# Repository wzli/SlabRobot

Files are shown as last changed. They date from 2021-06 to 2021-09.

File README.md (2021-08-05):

# Slab Robot
Work in progress...

## Mechanical Design
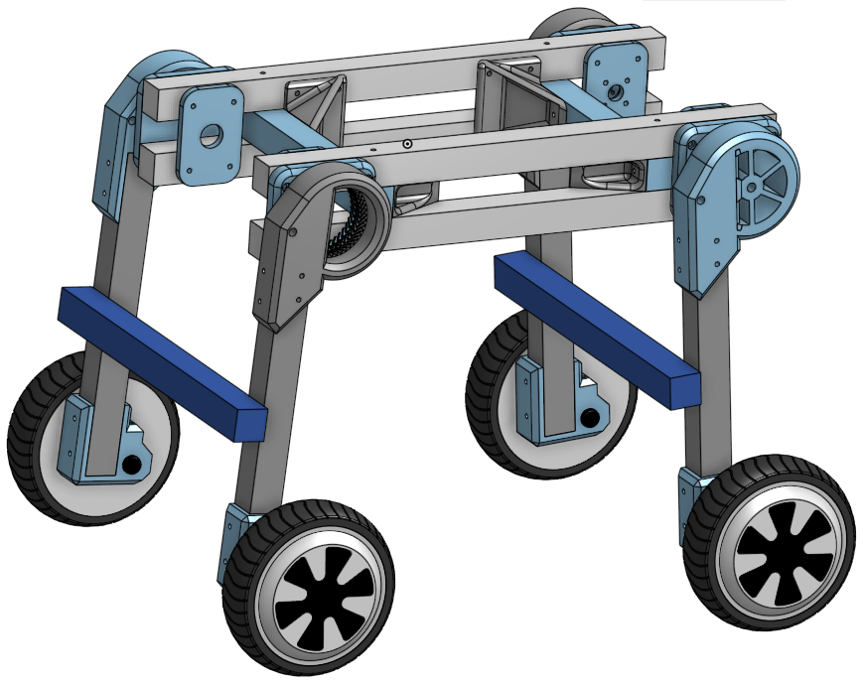
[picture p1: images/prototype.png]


[OnShape CAD Document](https://cad.onshape.com/documents/01b7bf47ac0296002ad3efc0/w/656ec7f127d0c64f6943908d/e/5454fd1cd4994d1435836e10)

## Simulation
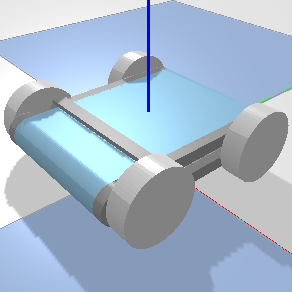
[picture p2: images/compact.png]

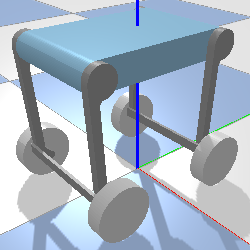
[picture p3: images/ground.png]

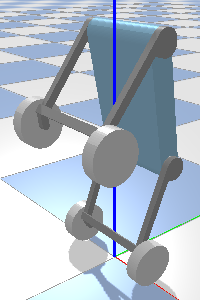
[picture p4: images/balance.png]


[Onshape to Robot](https://onshape-to-robot.readthedocs.io/) is used to generate robot simulation URDF files based on the concept assembly CAD.

```bash
# generate urdf
sudo apt install openscad meshlab # install system dependencies
pip install onshape-to-robot # install python application

# generate and output to urdf directory based on urdf/config.json
onshape-to-robot urdf
```

Run the following commands (or the equivalent on your system) to setup:

```bash
# install system dependencies
sudo apt install cmake gcc python3
# Install pytohn dependencies:
pip3 install -r requirements.txt

# Build libslab
mkdir libslab/build
(cd libslab/build && cmake .. && make)
```

To start, execute `./sim.py`. A connected USB gamepad is required.

The controls are:

- Home button resets simulation.
- Select button recenters camera.
- Left stick controls wheels.
  - X-axis controls turning velocity.
  - Y-axis controls forward velocity.
  - D-pad scaled by L-trigger maps to left stick controls.
- Right stick controls legs.
  - X-axis controls rotation of both legs in the same direction.
  - Y-axis controls rotation of both legs in different directions (when not balancing).
  - Y-axis controls body incline (when balancing).
  - Diagonal axis controls individual legs.
  - Buttons scaled by R-trigger maps to right stick controls.
- Holding R button maps right stick to leg position presets.
  - Up maps U preset.
  - Down maps to inverted U preset.
  - Left maps to fully unfolded preset.
  - Right maps to fully folded preset.
- Holding L button disables balance controller.
- Balance controller automatically engages when one pair of legs are detected to be off the ground.

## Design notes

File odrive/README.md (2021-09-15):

# ODrive Setup Guide

Tips on setting up Odrive (v3.6) on FW v5.2 complementary to the [Official Docs](https://docs.odriverobotics.com/).

# USB connection
See [Downloading and Installing Tools](https://docs.odriverobotics.com/#downloading-and-installing-tools).

- For linux, need to setup udev rules.
- For windows, need to use [zadig](https://zadig.akeo.ie) to setup *libusb-win32* driver.

# Firmware
Should first update to latest firmware by running `odrivetool dfu`.
See [docs](https://docs.odriverobotics.com/#firmware) for details.
If that runs into issues though, don't bother troubleshooting *dfu* it's way more simple and reliable to just build firmware and flash through STlink.

## Firmware Development
Refer to [docs](https://docs.odriverobotics.com/developer-guide), in summary:

- Install dependencies `gcc-arm-embedded, openocd, tup, etc`.
- `git clone https://github.com/odriverobotics/ODrive` and pull the latest release.
- Edit `Firmware/tup.config` and call `make` in Firmware directory.
- Connect STlink pins `GND, SWD, and SWC` and call `make flash`.
- DIP switch needs to be flipped to RUN instead of DFU inorder to flash.
- For clone boards, the call to `check_board_version()` in `Firmware/Board/v3/board.cpp` has to be disabed, otherwise it will intentionally spinlock during init from OTP mismatch.

# CAN Bus Configuration
See [CAN Protocol Docs](https://docs.odriverobotics.com/can-protocol).

- There is a built-in DIP switch that toggles the 120Ω termination resistor.
- Each axis is an independent endpoint, with their unique node ID configured by `odrv0.axis0.config.can.node_id = [0 - 0x3F]`.
- Set baudrate to 1Mbps `odrv0.can.config.baud_rate = 1000000`.
- Set encoder rate (for both axis) `odrv0.axis0.config.can.encoder_rate_ms = 10`.
- Set heartbeat rate (for both axis) `odrv0.axis0.config.can.heartbeat_rate_ms = 100`.
- Save and reboot `odrv0.save_configuration()`.

# End Stops
Documentation is provided at [Endstops guide](https://docs.odriverobotics.com/endstops). Refer to [ODrive pinout](https://docs.odriverobotics.com/pinout) to select which GPIOs to use.

```
// Open drain example setup
odrv0.config.gpio1_mode = GPIO_MODE_DIGITAL_PULL_UP
odrv0.axis0.min_endstop.config.enabled = True
odrv0.axis0.min_endstop.config.gpio_num = 1
odrv0.axis0.min_endstop.config.is_active_high = False
odrv0.save_configuration()

// homing example
odrv0.axis0.controller.config.homing_speed = 5 // -ve to change direction
odrv0.axis0.requested_state = AXIS_STATE_HOMING
```

# Setup
First follow [wiring guide](https://docs.odriverobotics.com/#wiring-up-the-odrive) to hook things up.
Then refer to [params guide](https://docs.odriverobotics.com/#configure-m0) to configure each axis.

- **Double check wiring things might burn if hooked up incorrectly!**
- **Always recalibrate motor and encoders after things have been plugged and unplugged!**

## A. System Configuration
1. Set max regen current according to battery `odrv0.config.max_regen_current = 5`.
1. `odrv0.config.dc_max_negative_current = -10`.
2. Enable brake resistor `odrv0.config.enable_brake_resistor = True`.
3. Set `odrv0.config.brake_resistance = 2` (value of power resistor that comes with kit).

## B. Calibrate Motor

1. Set `odrv0.axis0.motor.config.pole_pairs = X`.
Refer to params guide to determing number of pole pairs for the motor.
The hover board motors have 15 pole pairs, and BDUAV6384 motors has 7 pole pairs.
2. Set `odrv0.axis0.motor.config.torque_constant = 8.27/(motor KV)`
3. Call `odrv0.axis0.requested_state = AXIS_STATE_MOTOR_CALIBRATION` to perform motor calibration.
Check `odrv0.axis0.motor.error == 0` to confirm that calibration succeeded.
4. To save motor calibration set `odrv0.axis0.motor.config.pre_calibrated = True` and call `odrv0.save_configuration()`

## C. Calibrate Hall Sensor
1. Before starting refer to [pinout](https://docs.odriverobotics.com/encoders.html#hall-effect-encoders) to correctly hook up hall sensor wires.
2. Set the following configs:

 ```
// axis0
odrv0.axis0.encoder.config.mode = ENCODER_MODE_HALL
odrv0.axis0.encoder.config.cpr = odrv0.axis0.motor.config.pole_pairs * 6
odrv0.axis0.encoder.config.bandwidth = 100
odrv0.axis0.encoder.config.calib_scan_distance = 150
odrv0.config.gpio9_mode = GPIO_MODE_DIGITAL
odrv0.config.gpio10_mode = GPIO_MODE_DIGITAL
odrv0.config.gpio11_mode = GPIO_MODE_DIGITAL
// axis 1
odrv0.axis1.encoder.config.mode = ENCODER_MODE_HALL
odrv0.axis1.encoder.config.cpr = odrv0.axis0.motor.config.pole_pairs * 6
odrv0.axis1.encoder.config.bandwidth = 100
odrv0.axis1.encoder.config.calib_scan_distance = 150
odrv0.config.gpio12_mode = GPIO_MODE_DIGITAL
odrv0.config.gpio13_mode = GPIO_MODE_DIGITAL
odrv0.config.gpio14_mode = GPIO_MODE_DIGITAL
```
3. Run polarity calibration by calling `odrv0.axis0.requested_state = AXIS_STATE_ENCODER_HALL_POLARITY_CALIBRATION`. Check `odrv0.axis0.encoder.error == 0` to confirm that calibration succeeded.
4. Run calibration by calling `odrv0.axis0.requested_state = AXIS_STATE_ENCODER_OFFSET_CALIBRATION`. Check `odrv0.axis0.encoder.error == 0` to confirm that calibration succeeded.
5. To save encoder calibration set `odrv0.axis0.encoder.config.pre_calibrated = True` and call `odrv0.save_configuration()`.

## D. Tune Controller

Follow steps in  [tuning guide](https://docs.odriverobotics.com/control).

- Set `odrv0.axis0.controller.config.vel_limit` to below the max speed motor can spin given supply voltage.
Units are revolutions/second. This can be calculated approximaty `0.7 * supply voltage * KV / 60`. Eg for the 6384 motors its 33 rev/s @ 24V.
- Set `odrv0.axis0.motor.config.current_lim` depending on motor (to not burn it). The ODrive can  handle around 40A continous phase current without active cooling so recommend limiting to 50A max.
- Tune current control loop by adjusting `odrv0.axis0.motor.config.current_control_bandwidth` until the current response is stable. Can verify by sending speed or velocity setpoints and looking live plot of the measured phase current.
- Tune velocity control loop by sending velocity setpoint an viewing live plot of estimate.
  1. Set `odrv0.axis0.controller.config.vel_integrator_gain = 0`
  2. Bump up `odrv0.axis0.controller.config.vel_gain` to the point where there is ossilation the back down a bit.
  3. Bump up `odrv0.axis0.controller.config.vel_integrator_gain` until there is overshoot then back down a bit.
- Tune encoder bandwidth by sending velocity setpoints and viewing that the velocity feedback isn't too noisy. Sometimes might have to have high bandwith to prevent spinout even though there is noise.
- Tune position control loop by sending position setpoints and live ploting the feedback.
  - Bump up `odrv0.axis0.controller.config.pos_gain` until there is overshoot then back down a bit.
  - Make sure that the setpoint is not too far away from current `odrv0.axis0.encoder.pos_estimate`, otherwise the error compensation will be really large and the controller will send unrealistic velocities.

## Reference Configurations
### BDUAV6384
```
odrv0.axis0.motor.config.torque_constant = 8.27 / 120
odrv0.axis0.controller.config.vel_limit = 50
odrv0.axis0.motor.config.current_lim = 100
odrv0.axis0.motor.config.current_lim_margin = 20
odrv0.axis0.motor.config.requested_current_range = 120
odrv0.axis0.motor.config.current_control_bandwidth = 100
odrv0.axis0.controller.config.pos_gain = 2
odrv0.axis0.controller.config.vel_gain = 0.25
odrv0.axis0.controller.config.vel_integrator_gain = 0.4
odrv0.axis0.controller.config.control_mode = CONTROL_MODE_POSITION_CONTROL
```

### Hoverboard Motor
```
odrv0.axis0.motor.config.torque_constant = 8.27 / 16
odrv0.axis0.controller.config.vel_limit = 8
odrv0.axis0.motor.config.current_lim = 35
odrv0.axis0.motor.config.requested_current_range = 40
odrv0.axis0.motor.config.current_control_bandwidth = 200

odrv0.axis0.controller.config.pos_gain = 1
odrv0.axis0.controller.config.vel_gain = 0.3
odrv0.axis0.controller.config.vel_integrator_gain = 0.12
odrv0.axis0.controller.config.control_mode = CONTROL_MODE_VELOCITY_CONTROL
```

# Troubleshoot
If error occured, the error codes stored in the following fields:

```
odrv0.axis.error
odrv0.axis.motor.error
odrv0.axis.encoder.error
odrv0.axis.controller.error
```
Refer to [troubleshoot guide](https://docs.odriverobotics.com/troubleshooting#error-codes) to decipher the error string.
Once addressed, the error fields can be set to 0 to clear, and operation can be resumed by re-entering closed loop control
`odrv0.axis0.requested_state = AXIS_STATE_CLOSED_LOOP_CONTROL`. Also `odrv0.reboot()` will clear the errors as well.
## Error codes:
### ERROR_CURRENT_LIMIT_VIOLATION
This is a problem with the current control loop where it overshoots the current limit set.
Fix by decreasing `odrv0.axis0.motor.config.current_control_bandwidth` to make current control less aggressive.
Can also increase `odrv0.axis0.motor.config.current_lim_margin` to allow the overshoot without erroring out, but note overshoot shouldn't be more than 30% of target in this case the configured current limit.

### ERROR_DC_BUS_OVER_REGEN_CURRENT
This happens when the motor is requested to spin down too quickly. By default the back EMF is absorbed by the brake resistor, but if its too large the resistor will get saturated. To fix either reduce jerkyness of the motor, or hook up a battery as power source to absorb the regen current.
Usually it is safe to charge lipo batteries at 1-2C. Once the allowable regen current is known, configure with:

```
odrv0.config.max_regen_current = 5
odrv0.config.dc_max_negative_current = -5 # note this is negative the above
```

### ERROR_PHASE_RESISTANCE_OUT_OF_RANGE
Need to bump up `odrv0.axis0.motor.config.resistance_calib_max_voltage` if the phase resistance of the motor is large. This is the case with hoverboard motors.

```
resistance_calib_max_voltage > calibration_current * phase_resistance
resistance_calib_max_voltage < 0.5 * vbus_voltage
```
### ILLEGAL_SENSOR_STATE
It could be noise on the encoder lines that can be fixed by adding 47nF caps see [here](https://discourse.odriverobotics.com/t/encoder-error-error-illegal-hall-state/1047/7?u=madcowswe).
Also it could be the hall states are not what the firmware expects because older versions have hall states hardcoded. This is the case with the BDUAV6384 motors. Update to `>= fw-v0.5.2` to pull in the hall state detection routine to fix.

### AXIS_STATE_CLOSED_LOOP_CONTROL requested but idles without any errors
Last time I encountered this, the fix was to erase configuration and redo the setup proceedure. Restoring old config does not work.

### MOTOR_ERROR_UNKNOWN_TORQUE & MOTOR_ERROR_UNKNOWN_VOLTAGE_COMMAND & CONTROLLER_ERROR_SPINOUT_DETECTED
Encoder bandwidth is too low, and position estimates cannot keep with fact jerks and impacts.

# Common Commands

## Print Errors
```
dump_errors(odrv0)
```
## Idle
```
odrv0.axis0.requested_state = AXIS_STATE_IDLE
```
## Velocity Test
```
odrv0.axis0.controller.config.control_mode = CONTROL_MODE_VELOCITY_CONTROL
odrv0.axis0.requested_state = AXIS_STATE_CLOSED_LOOP_CONTROL
odrv0.axis0.controller.input_vel = 0
```
## Position Test
```
odrv0.axis0.controller.config.control_mode = CONTROL_MODE_POSITION_CONTROL
odrv0.axis0.requested_state = AXIS_STATE_CLOSED_LOOP_CONTROL
odrv0.axis0.controller.input_pos = 0
```
## Live Plotter
```
start_liveplotter(lambda: [odrv0.axis0.motor.current_control.Iq_measured])
start_liveplotter(lambda: [odrv0.axis0.controller.input_vel, odrv0.axis0.encoder.vel_estimate])
start_liveplotter(lambda: [odrv0.axis0.controller.input_pos, odrv0.axis0.encoder.pos_estimate])
```
## Backup and Restore
```
odrivetool backup-config myconfig.json
odrivetool restore-config myconfig.json
```
## Save Configuration
`odrv0.save_configuration()`
## Factory Reset
`odrv0.erase_configuration()`
## Reboot
`odrv0.reboot()`

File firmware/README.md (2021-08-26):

# Firmware Setup

## Hardware
### ESP32-CAM
- ***First check if VDD is connected to 5V or 3.3V***.
- remove resistors to flash LED, its the one right below the voltage selectors.

### PS3 Gamepad
Find the bluetooth MAC address of the ESP32 in UART prints during boot.

Bluetooth MAC

Then configure the PS3 gamepad to connect to that MAC address by following [Sixaxis USB pairing](https://help.ubuntu.com/community/Sixaxis#USB_Pairing).

Once MAC is configured. Press gamepad home button to turn on and connect.

*If gamepad disconnects, reconnect by holding home button to turn off and turn back on again. There is a known issue where reconnect only works on the second attempt.*

### CAN Troubleshoot
- Measure resistance across CANH and CANL to verify 60Ω of the combined termination resistors on each end.
- Check that all devices on the bus is configured to the same baudrate.

#### For ESP32 side refer to [CAN Peripheral Doc](https://docs.espressif.com/projects/esp-idf/en/latest/esp32s2/api-reference/peripherals/twai.html).
- Verify that the setup works using [Loopback Self Test](https://github.com/espressif/esp-idf/tree/master/examples/peripherals/twai/twai_self_test).
- Check that the correct message ID filters are applied.

#### For ODrive side refer to [CAN Protocol Doc](https://docs.odriverobotics.com/can-protocol).
- By default, constant heartbeat messages are sent at 10Hz. This can be verified by measuring voltage across CANH and CANL. The expected value is ~1.57V assuming equal distribution of 1's and 0's corresponding to differential voltages of 0V and 3.3V.
- CAN is turned off via setting :

- ```
  odrv0.config.enable_can_a = False
  odrv0.save_configuration()
  odrv0.reboot()
  ```
Then the expected differential voltage across CANH and CANL is either 0V or 3.3V.

- Check that the DIP switch for toggling termination resistor is set correctly.
- Check that all devices on bus is configured to a unique node ID.

#### For SN65HVD230 Module refer to [Datasheet](https://www.ti.com/lit/ds/symlink/sn65hvd230.pdf).
- It's basically a glorified comparator circuit. To test functionality, first apply HIGH and LOW on TX pin and verify differential voltage of 0 and VDD across CAN lines, then vice versa apply 0 and VDD differntial voltage across CAN lines and verify RX pin is driven HIGH and LOW.
- The modules includes a 120Ω termination resistor by default, desolder to remove.
- Doesn't require pullups unless GPIO is open-drain.
- 0.1uF decoupling capacitor recommended.
- Cheap chinese sourced parts may be fake and disfunctional so test them first.

# ESP32
Follow the getting started guide in
[Official ESP-IDF Docs](https://docs.espressif.com/projects/esp-idf/en/stable/esp32/) to setup firmware development enviroment. Alternatively
[ESP-IDF Docker](https://hub.docker.com/r/espressif/idf) provides everything preconfigured.

```bash
docker pull espressif/idf:release-v4.3
```

## Configure
`./idf.sh menuconfig`

### Options
- Compiler Options / Optimization Level
  - Optimize for performance (-O2)
- Component Config / Driver Configurations / TWAI configuration
  - Place TWAI ISR function into IRAM
- Component Config / ESP32-Specific / CPU frequency
  - 240 MHz
- Component Config / ESP32-Specific / Support for external, SPI-connected RAM
  - False / True (ESP32-CAM has 4MB PSRAM but CS pin on IO16 might be used)
- Component Config / FreeRTOS / Enable FreeRTOS to collect run time stats
  - True
- Component Config / FreeRTOS / Enable display of xCoreID in vTaskList
  - True
- Component Config / Core dump / Data destination
  - Flash
- Component Config / ESP System Settings / Panic handler behaviour
  - Print registers and halt (Invoke GDBStub breaks flash coredump)
- [PS3 controller config](https://github.com/jvpernis/esp32-ps3#configuring-your-project)

## Build
`./idf.sh build`

## Flash
- connect usb serial to UART pins
- ground IO0 pin
- `idf.sh -p PORT [-b BAUD] flash`

## Serial Monitor
`idf.py monitor`

# MPU6050

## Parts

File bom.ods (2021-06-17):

 |  |  |  |  | 952.9
Item | Type | Description | Quantity | Unit Price ($) | Price ($) | Source | Notes
ESP32-CAM | Electronic | ESP32 dev board | 1 | 7 | 7 | https://www.aliexpress.com/item/1005001706120772.html
GY-521 MPU6050 Module | Electronic | 6-DOF IMU | 1 | 3 | 3 | https://www.aliexpress.com/item/32304143704.html
SN65HVD230 CAN Module | Electronic | High speed CAN bus transceiver module | 1 | 2 | 2 | https://www.aliexpress.com/item/32865702099.html
Odrive V3.6 54V | Electronic | Dual Brushless Motor Controller | 3 | 100 | 300 | https://odriverobotics.com/shop/odrive-v36 https://www.aliexpress.com/item/4000756440841.html
6384 120KV Brushless Motor | Electronic |  | 2 | 60 | 120 | https://www.aliexpress.com/item/4000474554328.html
Hoverboard Hub Motor | Electronic |  | 4 | 70 | 280 | https://www.aliexpress.com/item/32651211455.html
10S 20Ah Lipo Battery | Electronic |  | 1 | 80 | 80 | https://www.aliexpress.com/item/1005001280420516.html
Prototye PCB (3cm x 7cm) | Electronic |  | 1 | 0.5 | 0.5 | https://www.aliexpress.com/item/32858804393.html
120 ohm Resistor | Electronic | For CAN bus termination | 1 |  |  |  | SN65HVD230 module has one built in
XT60 Connector Pair | Electronic
4mm Banana Plug Pair | Electronic
Wires
Heat Shrink
JST-XH connectors |  |  |  |  |  | https://www.aliexpress.com/item/1005001659802059.html
Limit Switch |  |  | 4 | 0.25 | 1 | https://www.aliexpress.com/item/32273125391.html
3030 Aluminum Extrusion 50cm | Mechanical |  | 4 | 10 | 40 | https://www.aliexpress.com/item/1005001607727629.html
3030 Aluminum Extrusion 30cm | Mechanical |  | 4 | 7 | 28 | https://www.aliexpress.com/item/1005001607727629.html
3030 Aluminum Extrusion 35cm | Mechanical |  | 2 | 6.5 | 13 | https://www.aliexpress.com/item/1005001607727629.html
3030 Aluminum Extrusion 25cm | Mechanical |  | 2 | 7.5 | 15 | https://www.aliexpress.com/item/1005001607727629.html
M4 3030 T-Nut | Mechanical |  | 150 | 0.2 | 30 | https://www.aliexpress.com/item/32964780472.html
M6 3030 T-Nut | Mechanical |  | 32 | 0.2 | 6.4 | https://www.aliexpress.com/item/32964780472.html
M6 10mm screw | Mechanical |  | 32 | 0.2 | 6.4 | https://www.aliexpress.com/item/10000150053486.html
Aluminum Bracket | Mechanical |  | 16 | 0.6 | 9.6 | https://www.aliexpress.com/item/33013635174.html
M3 Screw 30cm | Mechanical |  | 20 | 0.1 | 2 | https://www.aliexpress.com/item/10000150053486.html | For gear assembly
M8 10cm half thread bolt | Mechanical |  | 2 | 3 | 6 | https://www.aliexpress.com/item/32860422627.html
608 bearing | Mechanical |  | 6 | 0.5 | 3 | https://www.aliexpress.com/item/4000041280015.html
 |  |  |  |  |  |  |  | M3 6mm | M3 30mm | M4 10mm | M4 16mm | M4 18 | M4 30
Wheel Mount | PETG Printed Part | Attaches hub motor to legs | 4 |  |  | https://cad.onshape.com/documents/01b7bf47ac0296002ad3efc0/w/656ec7f127d0c64f6943908d/e/1f3cdadbdbd8b6e7c7be8cb7 | 5 X M4 16mm screws each |  |  |  | 20 |  | 8
Leg Mount | PLA Printed Part | Attaches leg to shoulder gears | 2 |  |  | https://cad.onshape.com/documents/01b7bf47ac0296002ad3efc0/w/656ec7f127d0c64f6943908d/e/f17f5007d16e7ec8a7ed1107 | 5 X M4 16mm screws each |  |  |  | 10
Leg Mount (Non Geared) | PETG Printed Part | Attaches leg to shoulder | 2 |  |  |  | 5 X M4 16mm screws each |  |  |  | 10
Shoulder Mount | PLA Printed Part | Attaches shoulder gears to chassis | 2 |  |  | https://cad.onshape.com/documents/01b7bf47ac0296002ad3efc0/w/656ec7f127d0c64f6943908d/e/3e013b284701bbb473a7c290 | 4 X M4 18mm screws each |  |  |  |  | 8
Shoulder Mount (Non Geared) | PETG Printed Part | Attaches shoulder to chassis | 2 |  |  |  | 4 X M4 18mm screws each |  |  |  |  | 8
Shoulder Mount Support | PETG Printed Part | Back side of shoulder mount | 2 |  |  |  | 4 X M4 16 mm screws each |  |  |  | 8
Right Angle Bracket | PETG Printed Part | Chassis corners | 4 |  |  | https://cad.onshape.com/documents/01b7bf47ac0296002ad3efc0/w/656ec7f127d0c64f6943908d/e/b7a7c45daeb7707e5d8554be | 6 X M4 10 mm screws each |  |  | 24
Motor Mount | ABS Printed Part |  | 2 |  |  | https://cad.onshape.com/documents/01b7bf47ac0296002ad3efc0/w/656ec7f127d0c64f6943908d/e/25adbbf539c089b718d4bf26 | 4 X M4 16 mm screws each |  |  |  | 8
Shaft Coupling | ABS Printed Part |  | 2 |  |  | https://cad.onshape.com/documents/01b7bf47ac0296002ad3efc0/w/656ec7f127d0c64f6943908d/e/b3e566b463c38dcfe41428a0 | 4 X M3 mm each |  | 8
Gear Set | PLA Printed Part |  | 2 |  |  | https://cad.onshape.com/documents/ed31ab88f277f15e29dfe781/w/7b86c19816d3b8349cc607b2/e/f7f94bc89e69a962ab54a434 | 10 X M3 30mm each |  | 20
Odrive Mount Left | ABS Printed Part |  | 3 |  |  | https://cad.onshape.com/documents/01b7bf47ac0296002ad3efc0/w/656ec7f127d0c64f6943908d/e/5d97cff1145f8e437ab64bce | 2 x M3 6mm screws + 1 x M4 10mm | 6 |  | 3
Odrive Mount Right | ABS Printed Part |  | 3 |  |  | https://cad.onshape.com/documents/01b7bf47ac0296002ad3efc0/w/656ec7f127d0c64f6943908d/e/5d97cff1145f8e437ab64bce | 2 x M3 6mm screws + 1 x M4 10mm | 6 |  | 3
 |  |  |  |  |  |  |  | 12 | 28 | 30 | 56 | 16 | 8
Have 60 x 16mm and 40 x 10mm

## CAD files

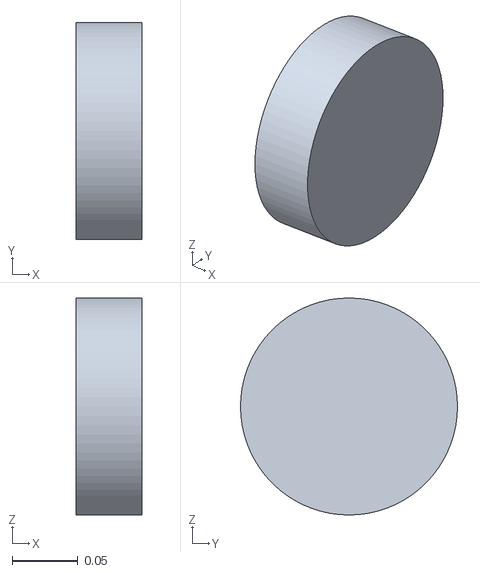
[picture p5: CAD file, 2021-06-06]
urdf/wheel.stl
0.05 x 0.165 x 0.165

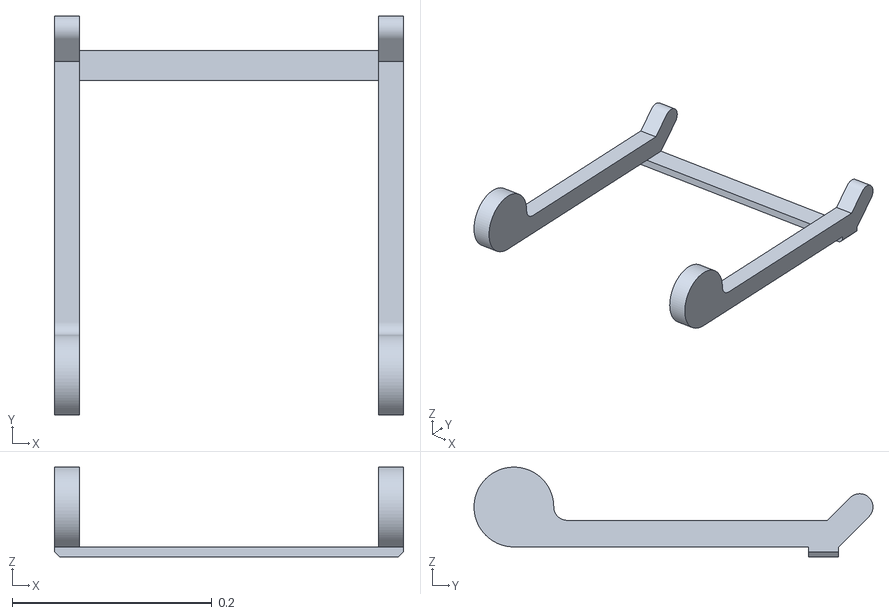
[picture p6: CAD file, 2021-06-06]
urdf/leg.stl
0.35 x 0.4 x 0.09

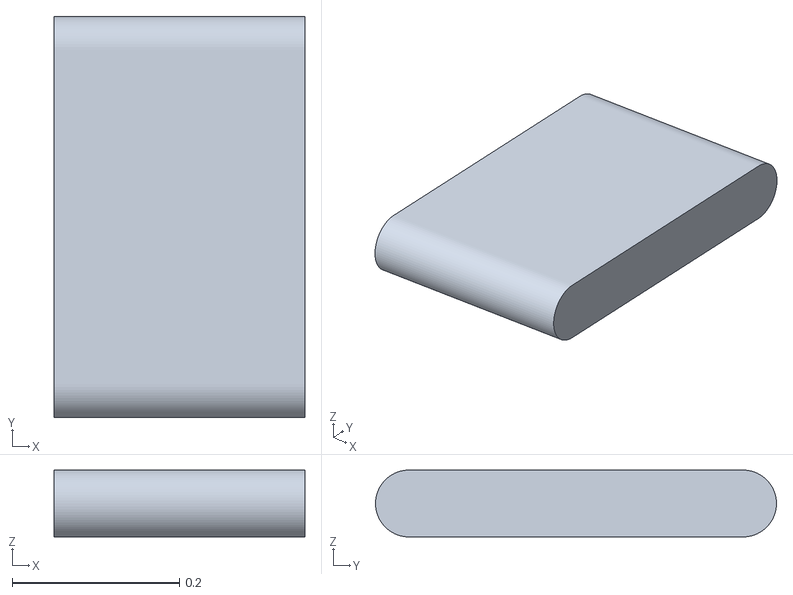
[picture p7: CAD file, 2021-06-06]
urdf/body.stl
0.3 x 0.48 x 0.08

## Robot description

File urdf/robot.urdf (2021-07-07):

<robot name="onshape">
<link name="body">
<visual>
<origin xyz="0 0 -0.04" rpy="3.14159 -5.03885e-29 -1.11022e-16" />
<geometry>
<mesh filename="package://body.stl"/>
</geometry>
<material name="body_material">
<color rgba="0.615686 0.811765 0.929412 1.0"/>
</material>
</visual>
<collision>
<origin xyz="0 0 -0.04" rpy="3.14159 -5.03885e-29 -1.11022e-16" />
<geometry>
<mesh filename="package://body.stl"/>
</geometry>
<material name="body_material">
<color rgba="0.615686 0.811765 0.929412 1.0"/>
</material>
</collision>
<inertial>
<origin xyz="-1.08364e-33 9.76058e-18 -0.04" rpy="0 0 0"/>
<mass value="7.22018" />
<inertia ixx="0.133175" ixy="2.12104e-17" ixz="-1.59622e-29" iyy="0.0578714" iyz="-6.09576e-29" izz="0.183606" />
</inertial>
</link>

<link name="leg">
<visual>
<origin xyz="0.2 0 0.15" rpy="1.5708 1.5708 0" />
<geometry>
<mesh filename="package://leg.stl"/>
</geometry>
<material name="leg_material">
<color rgba="0.647059 0.647059 0.647059 1.0"/>
</material>
</visual>
<collision>
<origin xyz="0.2 0 0.15" rpy="1.5708 1.5708 0" />
<geometry>
<mesh filename="package://leg.stl"/>
</geometry>
<material name="leg_material">
<color rgba="0.647059 0.647059 0.647059 1.0"/>
</material>
</collision>
<inertial>
<origin xyz="0.150043 0.019542 0.15" rpy="0 0 0"/>
<mass value="1.46202" />
<inertia ixx="0.0603673" ixy="-4.37547e-62" ixz="0.00199071" iyy="0.0253453" iyz="-1.01622e-63" izz="0.036191" />
</inertial>
</link>

<link name="wheel">
<visual>
<origin xyz="-0.146667 9.71445e-17 0.175" rpy="1.5708 1.5708 0" />
<geometry>
<mesh filename="package://wheel.stl"/>
</geometry>
<material name="wheel_material">
<color rgba="0.917647 0.917647 0.917647 1.0"/>
</material>
</visual>
<collision>
<origin xyz="-0.146667 9.71445e-17 0.175" rpy="1.5708 1.5708 0" />
<geometry>
<mesh filename="package://wheel.stl"/>
</geometry>
<material name="wheel_material">
<color rgba="0.917647 0.917647 0.917647 1.0"/>
</material>
</collision>
<inertial>
<origin xyz="-2.77556e-17 -1.79635e-17 -0.025" rpy="0 0 0"/>
<mass value="1.81751" />
<inertia ixx="0.00347125" ixy="8.5573e-35" ixz="-2.73834e-33" iyy="0.00618521" iyz="-3.37526e-65" izz="0.00347125" />
</inertial>
</link>

<joint name="front_left_wheel" type="revolute">
<origin xyz="0.346667 -1.11022e-16 -0.025" rpy="3.012e-15 1.23012e-14 0.0412877" />
<parent link="leg" />
<child link="wheel" />
<axis xyz="0 0 1"/>
<limit effort="1" velocity="20" />
<joint_properties friction="0.0"/>
</joint>

<link name="wheel_2">
<visual>
<origin xyz="-0.146667 1.17961e-16 0.175" rpy="1.5708 1.5708 0" />
<geometry>
<mesh filename="package://wheel.stl"/>
</geometry>
<material name="wheel_material">
<color rgba="0.917647 0.917647 0.917647 1.0"/>
</material>
</visual>
<collision>
<origin xyz="-0.146667 1.17961e-16 0.175" rpy="1.5708 1.5708 0" />
<geometry>
<mesh filename="package://wheel.stl"/>
</geometry>
<material name="wheel_material">
<color rgba="0.917647 0.917647 0.917647 1.0"/>
</material>
</collision>
<inertial>
<origin xyz="-2.77556e-17 2.85319e-18 -0.025" rpy="0 0 0"/>
<mass value="1.81751" />
<inertia ixx="0.00347125" ixy="7.01779e-34" ixz="0" iyy="0.00618521" iyz="0" izz="0.00347125" />
</inertial>
</link>

<joint name="front_right_wheel" type="revolute">
<origin xyz="0.346667 -1.11022e-16 0.325" rpy="-3.14159 2.46677e-14 -2.63678e-15" />
<parent link="leg" />
<child link="wheel_2" />
<axis xyz="0 0 1"/>
<limit effort="1" velocity="20" />
<joint_properties friction="0.0"/>
</joint>

<joint name="front_leg" type="revolute">
<origin xyz="0.15 -0.2 -0.04" rpy="1.5708 -8.28304e-30 -1.5708" />
<parent link="body" />
<child link="leg" />
<axis xyz="0 0 1"/>
<limit effort="1" velocity="20" lower="-3.14159" upper="3.14159"/>
<joint_properties friction="0.0"/>
</joint>

<link name="leg_2">
<visual>
<origin xyz="0.2 0 0.15" rpy="1.5708 1.5708 0" />
<geometry>
<mesh filename="package://leg.stl"/>
</geometry>
<material name="leg_material">
<color rgba="0.647059 0.647059 0.647059 1.0"/>
</material>
</visual>
<collision>
<origin xyz="0.2 0 0.15" rpy="1.5708 1.5708 0" />
<geometry>
<mesh filename="package://leg.stl"/>
</geometry>
<material name="leg_material">
<color rgba="0.647059 0.647059 0.647059 1.0"/>
</material>
</collision>
<inertial>
<origin xyz="0.150043 0.019542 0.15" rpy="0 0 0"/>
<mass value="1.46202" />
<inertia ixx="0.0603673" ixy="1.09028e-57" ixz="0.00199071" iyy="0.0253453" iyz="2.53215e-59" izz="0.036191" />
</inertial>
</link>

<link name="wheel_3">
<visual>
<origin xyz="-0.146667 9.71445e-17 0.175" rpy="1.5708 1.5708 0" />
<geometry>
<mesh filename="package://wheel.stl"/>
</geometry>
<material name="wheel_material">
<color rgba="0.917647 0.917647 0.917647 1.0"/>
</material>
</visual>
<collision>
<origin xyz="-0.146667 9.71445e-17 0.175" rpy="1.5708 1.5708 0" />
<geometry>
<mesh filename="package://wheel.stl"/>
</geometry>
<material name="wheel_material">
<color rgba="0.917647 0.917647 0.917647 1.0"/>
</material>
</collision>
<inertial>
<origin xyz="2.77556e-17 -1.79635e-17 -0.025" rpy="0 0 0"/>
<mass value="1.81751" />
<inertia ixx="0.00347125" ixy="-1.13737e-34" ixz="-2.33989e-36" iyy="0.00618521" iyz="-2.55138e-68" izz="0.00347125" />
</inertial>
</link>

<joint name="back_left_wheel" type="revolute">
<origin xyz="0.346667 -1.11022e-16 -0.025" rpy="2.10385e-17 -2.31218e-16 3.05433" />
<parent link="leg_2" />
<child link="wheel_3" />
<axis xyz="0 0 1"/>
<limit effort="1" velocity="20" />
<joint_properties friction="0.0"/>
</joint>

<link name="wheel_4">
<visual>
<origin xyz="-0.146667 1.66533e-16 0.175" rpy="1.5708 1.5708 0" />
<geometry>
<mesh filename="package://wheel.stl"/>
</geometry>
<material name="wheel_material">
<color rgba="0.917647 0.917647 0.917647 1.0"/>
</material>
</visual>
<collision>
<origin xyz="-0.146667 1.66533e-16 0.175" rpy="1.5708 1.5708 0" />
<geometry>
<mesh filename="package://wheel.stl"/>
</geometry>
<material name="wheel_material">
<color rgba="0.917647 0.917647 0.917647 1.0"/>
</material>
</collision>
<inertial>
<origin xyz="8.32667e-17 5.14254e-17 -0.025" rpy="0 0 0"/>
<mass value="1.81751" />
<inertia ixx="0.00347125" ixy="4.57432e-34" ixz="-1.71146e-34" iyy="0.00618521" iyz="-6.86696e-19" izz="0.00347125" />
</inertial>
</link>

<joint name="back_right_wheel" type="revolute">
<origin xyz="0.346667 -1.11022e-16 0.325" rpy="-3.14159 -1.13436e-16 0.785398" />
<parent link="leg_2" />
<child link="wheel_4" />
<axis xyz="0 0 1"/>
<limit effort="1" velocity="20" />
<joint_properties friction="0.0"/>
</joint>

<joint name="back_leg" type="revolute">
<origin xyz="0.15 0.2 -0.04" rpy="-1.5708 2.52435e-28 1.5708" />
<parent link="body" />
<child link="leg_2" />
<axis xyz="0 0 1"/>
<limit effort="1" velocity="20" lower="-3.14159" upper="3.14159"/>
<joint_properties friction="0.0"/>
</joint>


</robot>

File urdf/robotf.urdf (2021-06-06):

<?xml version="1.0"?>
<robot name="onshape">
  <link name="body">
    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
    <inertial>
      <origin xyz="0 0 0" rpy="0 0 0"/>
      <mass value="0"/>
      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
    </inertial>
  </link>
  <link name="leg">
    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
    <inertial>
      <origin xyz="0 0 0" rpy="0 0 0"/>
      <mass value="0"/>
      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
    </inertial>
  </link>
  <link name="wheel">
    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
    <inertial>
      <origin xyz="0 0 0" rpy="0 0 0"/>
      <mass value="0"/>
      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
    </inertial>
  </link>
  <joint name="front_right_wheel" type="revolute">
    <origin xyz="0.346667 -1.66533e-16 -0.025" rpy="3.85237e-16 -1.77554e-16 -1.62403"/>
    <parent link="leg"/>
    <child link="wheel"/>
    <axis xyz="0 0 1"/>
    <limit effort="1" velocity="20"/>
    <joint_properties friction="0.0"/>
  </joint>
  <link name="wheel_2">
    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
    <inertial>
      <origin xyz="0 0 0" rpy="0 0 0"/>
      <mass value="0"/>
      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
    </inertial>
  </link>
  <joint name="front_left_wheel" type="revolute">
    <origin xyz="0.346667 -8.32667e-17 0.325" rpy="3.14159 -2.52787e-16 1.5708"/>
    <parent link="leg"/>
    <child link="wheel_2"/>
    <axis xyz="0 0 1"/>
    <limit effort="1" velocity="20"/>
    <joint_properties friction="0.0"/>
  </joint>
  <joint name="front_leg" type="revolute">
    <origin xyz="-0.15 -0.2 -0.04" rpy="-1.5708 1.53677 -1.5708"/>
    <parent link="body"/>
    <child link="leg"/>
    <axis xyz="0 0 1"/>
    <limit effort="1" velocity="20" lower="-3.14159" upper="3.14159"/>
    <joint_properties friction="0.0"/>
  </joint>
  <link name="leg_2">
    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
    <inertial>
      <origin xyz="0 0 0" rpy="0 0 0"/>
      <mass value="0"/>
      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
    </inertial>
  </link>
  <link name="wheel_3">
    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
    <inertial>
      <origin xyz="0 0 0" rpy="0 0 0"/>
      <mass value="0"/>
      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
    </inertial>
  </link>
  <joint name="back_right_wheel" type="revolute">
    <origin xyz="0.346667 -5.55112e-17 -0.025" rpy="2.65801e-15 1.23315e-14 -1.52951"/>
    <parent link="leg_2"/>
    <child link="wheel_3"/>
    <axis xyz="0 0 1"/>
    <limit effort="1" velocity="20"/>
    <joint_properties friction="0.0"/>
  </joint>
  <link name="wheel_4">
    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
    <inertial>
      <origin xyz="0 0 0" rpy="0 0 0"/>
      <mass value="0"/>
      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
    </inertial>
  </link>
  <joint name="back_left_wheel" type="revolute">
    <origin xyz="0.346667 -1.11022e-16 0.325" rpy="3.14159 -2.46833e-14 1.5708"/>
    <parent link="leg_2"/>
    <child link="wheel_4"/>
    <axis xyz="0 0 1"/>
    <limit effort="1" velocity="20"/>
    <joint_properties friction="0.0"/>
  </joint>
  <joint name="back_leg" type="revolute">
    <origin xyz="-0.15 0.2 -0.04" rpy="2.70626e-17 1.5708 0"/>
    <parent link="body"/>
    <child link="leg_2"/>
    <axis xyz="0 0 1"/>
    <limit effort="1" velocity="20" lower="-3.14159" upper="3.14159"/>
    <joint_properties friction="0.0"/>
  </joint>
</robot>

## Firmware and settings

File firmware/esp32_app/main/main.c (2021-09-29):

#include "freertos/FreeRTOS.h"
#include "freertos/task.h"
#include "freertos/timers.h"
#include "freertos/queue.h"

#include "esp_err.h"
#include "esp_log.h"
#include "esp_vfs_fat.h"
#include "esp_wifi.h"
#include "esp_http_server.h"
#include "esp_bt_device.h"
#include "lwip/sockets.h"
#include "driver/i2c.h"
#include "driver/gpio.h"
#include "driver/sdmmc_host.h"
#include "driver/twai.h"
#include "nvs_flash.h"
#include "sdkconfig.h"

#include "odrive_can.h"
#include "ps3.h"
#include "slab.h"

//------------------------------------------------------------------------------
// constants

#define PIN_LED 33

#if 1
#define PIN_SDA 13
#define PIN_CLK 16

#define PIN_CAN_TX 12
#define PIN_CAN_RX 4
#else
#define PIN_SDA 22
#define PIN_CLK 23

#define PIN_CAN_TX 32
#define PIN_CAN_RX 25
#endif

#define CAN_BAUD_RATE TWAI_TIMING_CONFIG_1MBITS

#define TELEMETRY_TASK_INTERVAL_TICKS 5
#define LED_HEARTBEAT_DOT_TICKS 20
#define MOTOR_HOMING_TIMEOUT_TICKS 50
#define MOTOR_COMMS_TIMEOUT_TICKS 50
#define IMU_COMMS_TIMEOUT_TICKS 50
#define GAMEPAD_COMMS_TIMEOUT_TICKS 50

#define N_MOTORS 6
static const float MOTOR_GEAR_RATIOS[N_MOTORS] = {-26, 26, -1, 1, -1, 1};

static const SlabConfig SLAB_CONFIG = {
        .max_wheel_speed = 50.0f,          // rads/s
        .wheel_diameter = 0.165f,          // m
        .wheel_distance = 0.425f,          // m
        .body_length = 0.380f,             // m
        .leg_length = 0.294f,              // m
        .max_leg_position = M_PI * 3 / 4,  // rad
        .min_leg_position = -M_PI,         // rad
        .imu_axis_remap = {AXIS_REMAP_X, AXIS_REMAP_Y, AXIS_REMAP_Z},
        .joystick_threshold = 10,       // 0 - 255
        .ground_rise_threshold = 0.08,  // m
        .ground_fall_threshold = 0.04,  // m
        .incline_p_gain = 100.0f,
        .speed_p_gain = 0.3f,
        .speed_i_gain = 0.0005f,
};

static const wifi_ap_config_t WIFI_AP_CONFIG = {
        .ssid = "slab_robot",
        .ssid_len = 10,
        .channel = 1,
        .password = "",
        .max_connection = 3,
        .authmode = WIFI_AUTH_OPEN,
};

static const uint16_t UDP_OUT_PORT = 9870;
static const uint16_t UDP_IN_PORT = 9871;

//------------------------------------------------------------------------------
// typedefs

typedef struct {
    bool homing_required_front : 1;
    bool homing_required_back : 1;
    bool estop : 1;
    bool can_error : 1;
    bool motor_error : 1;
    bool motor_comms_timeout : 1;
    bool imu_comms_timeout : 1;
    bool gamepad_comms_timeout : 1;
} AppErrorFlags;

#define TYPEDEF_AppError(X, _) \
    X(uint32_t, code, )        \
    _(AppErrorFlags, flags, )
MXGEN(union, AppError)

#define TYPEDEF_ErrorCounter(X, _) \
    _(int32_t, running, )          \
    X(int32_t, total, )
MXGEN(struct, ErrorCounter)

// keep the same layout as twai_status_info_t
// rx_overrun_count exist only in espidf > 4.3
#define TYPEDEF_CanStatus(X, _)      \
    X(uint32_t, state, )             \
    X(uint32_t, msgs_to_tx, )        \
    X(uint32_t, msgs_to_rx, )        \
    X(uint32_t, tx_error_counter, )  \
    X(uint32_t, rx_error_counter, )  \
    X(uint32_t, tx_failed_counter, ) \
    X(uint32_t, rx_missed_count, )   \
    X(uint32_t, rx_overrun_count, )  \
    X(uint32_t, arb_loss_count, )    \
    X(uint32_t, bus_error_count, )
MXGEN(struct, CanStatus)

// keep the same layout as ODriveAxis
#define TYPEDEF_ODriveStatus(X, _)     \
    X(uint64_t, motor_error, )         \
    X(uint32_t, encoder_error, )       \
    _(uint32_t, sensorless_error, )    \
    X(uint32_t, axis_error, )          \
    X(uint32_t, axis_state, )          \
    _(int32_t, encoder_shadow_count, ) \
    _(int32_t, encoder_count_cpr, )    \
    X(float, encoder_position, )       \
    X(float, encoder_velocity, )
MXGEN(struct, ODriveStatus)

#define TYPEDEF_MotorStatus(X, _) \
    X(ODriveStatus, status, )     \
    _(ODriveAxis, odrive, )
MXGEN(union, MotorStatus)

#define TYPEDEF_AppStatus(X, _)                     \
    X(double, timestamp, )                          \
    X(Slab, slab, )                                 \
    X(CanStatus, can, )                             \
    X(MotorStatus, motors, [N_MOTORS])              \
    X(ErrorCounter, motor_comms_missed, [N_MOTORS]) \
    X(ErrorCounter, imu_comms_missed, )             \
    X(GamepadMsg, gamepad, )                        \
    X(uint32_t, gamepad_tick, )                     \
    X(AppError, error, )
MXGEN(struct, AppStatus)

typedef struct Imu Imu;

typedef struct {
    uint64_t led_pattern;
    int32_t dir_idx;
    TaskHandle_t control_task;
    TaskHandle_t telemetry_task;
    TimerHandle_t heartbeat_timer;
    TimerHandle_t homing_timer;
    QueueHandle_t status_in_queue;
    QueueHandle_t status_out_queue;
    Imu* imu;
    AppStatus status;
} App;

//------------------------------------------------------------------------------
// helper functions

#define RTOS_ERROR_CHECK(ERR) ESP_ERROR_CHECK((ERR) -pdPASS)

#define CAN_ERROR_CHECK(APP, ERR) \
    (app)->status.error.flags.can_error |= ESP_ERROR_CHECK_WITHOUT_ABORT(ERR)

static int error_counter_update(ErrorCounter* counter, int error_count) {
    counter->total += error_count;
    return counter->running = error_count ? counter->running + error_count : 0;
}

static FRESULT f_write_line(FIL* file, char* text_buf, int len) {
    text_buf[len] = '\n';
    text_buf[++len] = '\0';
    uint32_t bytes_written = 0;
    return f_write(file, text_buf, len, &bytes_written);
}

static FIL* file_create(const char* file_name) {
    FIL* file = malloc(sizeof(FIL));
    assert(file);
    assert(file_name);
    FRESULT fresult = f_open(file, file_name, FA_WRITE | FA_CREATE_NEW);
    if (fresult == FR_OK) {
        ESP_LOGI(pcTaskGetName(NULL), "f_open %s success", file_name);
        return file;
    } else {
        free(file);
        ESP_LOGW(pcTaskGetName(NULL), "failed to f_open %s error %d", file_name, fresult);
        return NULL;
    }
}

static int dir_create(const char* dir_name) {
    FRESULT fresult;
    char text_buf[16];
    int dir_idx = 0;
    do {
        sprintf(text_buf, "%s%d", dir_name, dir_idx);
        fresult = f_mkdir(text_buf);
    } while (FR_EXIST == fresult && ++dir_idx);
    if (fresult != FR_OK) {
        ESP_LOGW(pcTaskGetName(NULL), "f_mkdir sdcard/%s error %d", text_buf, fresult);
        return -1;
    }
    ESP_LOGI(pcTaskGetName(NULL), "f_mkdir sdcard/%s success", text_buf);
    return dir_idx;
}

static int print_heap_info(char* buf, const char* name, uint32_t capabilities) {
    multi_heap_info_t heap_info;
    heap_caps_get_info(&heap_info, capabilities);
    return sprintf(buf,
            "\n%s Heap Info\n"
            "total free bytes \t\t%d\n"
            "total allocated bytes \t\t%d\n"
            "largest free block \t\t%d\n"
            "minimum free bytes \t\t%d\n"
            "allocated blocks \t\t%d\n"
            "free blocks \t\t\t%d\n"
            "total blocks \t\t\t%d\n",
            name, heap_info.total_free_bytes, heap_info.total_allocated_bytes,
            heap_info.largest_free_block, heap_info.minimum_free_bytes, heap_info.allocated_blocks,
            heap_info.free_blocks, heap_info.total_blocks);
}

static esp_err_t parse_request_param(httpd_req_t* req, const char* param_name, char* param) {
    size_t buf_len = httpd_req_get_url_query_len(req) + 1;
    if (buf_len < 2 || (httpd_req_get_url_query_str(req, param, buf_len) != ESP_OK) ||
            (httpd_query_key_value(param, param_name, param, 32) != ESP_OK)) {
        return ESP_FAIL;
    }
    return ESP_OK;
}

//------------------------------------------------------------------------------
// input and feedback functions

extern Imu* imu_create();
extern bool imu_read(Imu* imu, ImuMsg* imu_msg);

static void ps3_gamepad_led_update(AppError app_error) {
    ps3_cmd_t cmd = {0};
    cmd.led1 = true;
    cmd.led2 = app_error.flags.homing_required_front || app_error.flags.homing_required_back;
    cmd.led3 = app_error.flags.estop;
    cmd.led4 = app_error.code > 7;
    if (app_error.code > 3) {
        cmd.rumble_left_intensity = 255;
        cmd.rumble_right_intensity = 255;
        cmd.rumble_left_duration = 30;
        cmd.rumble_right_duration = 30;
    }
    ps3Cmd(cmd);
}

static void motors_homing_request(App* app) {
    for (int i = 0; i < 2; ++i) {
        // only send request if homing required and not already homing
        static const uint32_t state = ODRIVE_AXIS_STATE_HOMING;
        if (app->status.error.code & (1 << i) &&
                app->status.motors[i].status.axis_state != state) {
            CAN_ERROR_CHECK(app,
                    odrive_send_command(i, ODRIVE_CMD_SET_REQUESTED_STATE, &state, sizeof(state)));
            // start homing timer to detect timeout
            RTOS_ERROR_CHECK(xTimerStart(app->homing_timer, 0));
        }
    }
}

static void motors_homing_complete_callback(
        uint8_t axis_id, ODriveAxisState new_state, ODriveAxisState old_state, void* context) {
    assert(axis_id < 2);
    App* app = (App*) context;
    // reset homing required error when state transitions from HOMING to IDLE
    if (old_state == ODRIVE_AXIS_STATE_HOMING && new_state == ODRIVE_AXIS_STATE_IDLE) {
        app->status.error.code &= ~(1 << axis_id);
        app->status.slab.input.leg_positions[axis_id] = -M_PI;
        app->status.slab.motors[axis_id].input =
                (MotorInput){-M_PI, 0, 0, MOTOR_CONTROL_MODE_POSITION};
        app->status.slab.motors[axis_id].estimate = (MotorEstimate){-M_PI, 0};
        ps3_gamepad_led_update(app->status.error);
    }
}

static void motors_homing_timeout_callback(TimerHandle_t timer) {
    App* app = (App*) pvTimerGetTimerID(timer);
    for (int i = 0; i < 2; ++i) {
        // assume that homing is complete if there are no errors after a timeout
        // this is required because homing complete callback won't trigger if motors start homed
        const ODriveStatus* odrive = &app->status.motors[i].status;
        if (app->status.error.code & (1 << i) && odrive->axis_state == ODRIVE_AXIS_STATE_IDLE &&
                !(odrive->axis_error & ~ODRIVE_AXIS_ERROR_MIN_ENDSTOP_PRESSED) &&
                !odrive->motor_error && !odrive->encoder_error) {
            motors_homing_complete_callback(
                    i, ODRIVE_AXIS_STATE_IDLE, ODRIVE_AXIS_STATE_HOMING, app);
        }
    }
}

static void motors_input_update(App* app) {
    for (int i = 0; i < N_MOTORS; ++i) {
        const ODriveStatus* odrive = &app->status.motors[i].status;
        const MotorMsg* motor = &app->status.slab.motors[i];
        // clear endstop errors if the command is in the centering direction
        if ((odrive->axis_error == ODRIVE_AXIS_ERROR_MIN_ENDSTOP_PRESSED &&
                    motor->input.position >= motor->estimate.position &&
                    motor->input.velocity >= 0 && motor->input.torque >= 0) ||
                (odrive->axis_error == ODRIVE_AXIS_ERROR_MAX_ENDSTOP_PRESSED &&
                        motor->input.position <= motor->estimate.position &&
                        motor->input.velocity <= 0 && motor->input.torque <= 0)) {
            CAN_ERROR_CHECK(app, odrive_send_command(i, ODRIVE_CMD_CLEAR_ERRORS, NULL, 0));
        }
        // request closed loop control state if not already
        static const uint32_t state = ODRIVE_AXIS_STATE_CLOSED_LOOP_CONTROL;
        if (odrive->axis_state != state) {
            CAN_ERROR_CHECK(app,
                    odrive_send_command(i, ODRIVE_CMD_SET_REQUESTED_STATE, &state, sizeof(state)));
        }
        // send different motor commands depending on desired control mode
        // assume that the odrive is preconfigured to the correct mode
        // scale by gear ratio then change radians to cycles
        switch (motor->input.control_mode) {
            case MOTOR_CONTROL_MODE_POSITION: {
                const ODriveInputPosition input_pos = {
                        (motor->input.position + M_PI) * MOTOR_GEAR_RATIOS[i] / (2 * M_PI),
                        1000 * motor->input.velocity * MOTOR_GEAR_RATIOS[i] / (2 * M_PI),
                        1000 * motor->input.torque / MOTOR_GEAR_RATIOS[i]};
                CAN_ERROR_CHECK(app, odrive_send_command(i, ODRIVE_CMD_SET_INPUT_POS, &input_pos,
                                             sizeof(input_pos)));
                break;
            }
            case MOTOR_CONTROL_MODE_VELOCITY: {
                const ODriveInputVelocity input_vel = {
                        motor->input.velocity * MOTOR_GEAR_RATIOS[i] / (2 * M_PI),
                        motor->input.torque / MOTOR_GEAR_RATIOS[i]};
                CAN_ERROR_CHECK(app, odrive_send_command(i, ODRIVE_CMD_SET_INPUT_VEL, &input_vel,
                                             sizeof(input_vel)));
                break;
            }
            default:
                assert(0 && "motor control mode not implemented");
        }
    }
}

static esp_err_t motors_feedback_update(App* app) {
    ODriveAxis* odrives = &app->status.motors->odrive;
    // clear updates flags
    for (int i = 0; i < N_MOTORS; ++i) {
        odrives[i].updates = (ODriveUpdates){0};
    }
    // fetch updates
    esp_err_t rx_error = odrive_receive_updates(odrives, N_MOTORS);
    app->status.error.flags.motor_comms_timeout = false;
    for (int i = 0; i < N_MOTORS; ++i) {
        // check for motor comms timeout
        const uint8_t* updated = (uint8_t*) &odrives[i].updates;
        if (error_counter_update(&app->status.motor_comms_missed[i], *updated == 0) >
                MOTOR_COMMS_TIMEOUT_TICKS) {
            app->status.error.flags.motor_comms_timeout = true;
            // reset velocity and current estimates on timeout
            odrives[i].encoder_estimates.velocity = 0;
            odrives[i].sensorless_estimates.velocity = 0;
            odrives[i].iq.measured = 0;
        }
        // check for motor errors (excluding endstop reached)
        if ((odrives[i].updates.heartbeat &&
                    (odrives[i].heartbeat.axis_error & ~ODRIVE_AXIS_ERROR_WATCHDOG_TIMER_EXPIRED &
                            ~ODRIVE_AXIS_ERROR_MIN_ENDSTOP_PRESSED &
                            ~ODRIVE_AXIS_ERROR_MAX_ENDSTOP_PRESSED)) ||
                (odrives[i].updates.motor_error && odrives[i].motor_error) ||
                (odrives[i].updates.encoder_error && odrives[i].encoder_error)) {
            app->status.error.flags.motor_error = true;
        }
        // convert odrive interface to motor interface
        // change cycles to radians then scale by gear ratio
        if (odrives[i].updates.encoder_estimates) {
            app->status.slab.motors[i].estimate.position =
                    2 * M_PI * odrives[i].encoder_estimates.position / MOTOR_GEAR_RATIOS[i] - M_PI;
            app->status.slab.motors[i].estimate.velocity =
                    2 * M_PI * odrives[i].encoder_estimates.velocity / MOTOR_GEAR_RATIOS[i];
        }
    }
    return rx_error;
}

static esp_err_t motors_error_request(uint32_t tick) {
    // send a different error request command every tick
    uint8_t axis_id = (tick / 2) % N_MOTORS;
    uint8_t cmd_id = tick & 1 ? ODRIVE_CMD_GET_MOTOR_ERROR : ODRIVE_CMD_GET_ENCODER_ERROR;
    return odrive_send_get_command(axis_id, cmd_id);
}

static void motors_clear_errors(App* app) {
    app->status.error.flags.motor_error = false;
    app->status.error.flags.can_error = false;
    for (int i = 0; i < N_MOTORS; ++i) {
        CAN_ERROR_CHECK(app, odrive_send_command(i, ODRIVE_CMD_CLEAR_ERRORS, NULL, 0));
    }
}

static void motors_init(App* app) {
    motors_clear_errors(app);
    // wait for errors to clear
    vTaskDelay(1);
    // homing is required for legs only
    for (int i = 0; i < 2; ++i) {
        app->status.error.code |= 1 << i;
        app->status.motors[i].odrive.state_transition_callback = motors_homing_complete_callback;
        app->status.motors[i].odrive.state_transition_context = app;
    }
    // create motor homing timer
    app->homing_timer = xTimerCreate("homing_timer", MOTOR_HOMING_TIMEOUT_TICKS, false, app,
            motors_homing_timeout_callback);
    assert(app->homing_timer);
}

//------------------------------------------------------------------------------
// task functions

static void led_heartbeat_callback(TimerHandle_t timer) {
    App* app = (App*) pvTimerGetTimerID(timer);
    if (!app->led_pattern) {
        int idx = 4;
        for (int i = 0; i < 8; ++i) {
            if (app->status.error.code & (1 << i)) {
                app->led_pattern |= 0x7ULL << idx;
                idx += 4;
            } else {
                app->led_pattern |= 1ULL << idx;
                idx += 2;
            }
        }
    }
    ESP_ERROR_CHECK(gpio_set_level(PIN_LED, !(app->led_pattern & 1)));
    app->led_pattern >>= 1;
}

static void ps3_gamepad_callback(void* pvParameters, ps3_t ps3_state, ps3_event_t ps3_event) {
    App* app = (App*) pvParameters;
    // parse gamepad message
    GamepadMsg* gamepad = &app->status.gamepad;
    memcpy(&gamepad->buttons, &ps3_state.button, 2);
    gamepad->left_stick.x = ps3_state.analog.stick.lx;
    gamepad->left_stick.y = ps3_state.analog.stick.ly;
    gamepad->right_stick.x = ps3_state.analog.stick.rx;
    gamepad->right_stick.y = ps3_state.analog.stick.ry;
    gamepad->left_trigger = ps3_state.analog.button.l2;
    gamepad->right_trigger = ps3_state.analog.button.r2;
    // update timestamp
    app->status.gamepad_tick = xTaskGetTickCount();
    // flip balance trigger
    gamepad->buttons ^= GAMEPAD_BUTTON_L1;
}
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
void app_main(void) {
    // init peripherals
    can_init();
    i2c_init();
    led_init();
    wifi_init();
    ps3_init();
    sdcard_init();
    // init app
    static App app = {0};
    app.status.slab.config = SLAB_CONFIG;
    app.imu = imu_create();
    motors_init(&app);
    httpd_init(&app);
    ps3SetEventObjectCallback(&app, ps3_gamepad_callback);
    esp_log_level_set("PS3_L2CAP", ESP_LOG_WARN);
    app.dir_idx = dir_create("slab");
    app.status_in_queue = xQueueCreate(2, sizeof(AppStatus*));
    app.status_out_queue = xQueueCreate(2, sizeof(AppStatus*));
    // init tasks
    RTOS_ERROR_CHECK(xTaskCreatePinnedToCore(
            telemetry_loop, "telemetry_loop", 3 * 2048, &app, 1, &app.telemetry_task, 0));
    RTOS_ERROR_CHECK(xTaskCreatePinnedToCore(
            control_loop, "control_loop", 3 * 2048, &app, 9, &app.control_task, 1));
    app.heartbeat_timer = xTimerCreate(
            "heartbeat_timer", LED_HEARTBEAT_DOT_TICKS, true, &app, led_heartbeat_callback);
    assert(app.heartbeat_timer);
    RTOS_ERROR_CHECK(xTimerStart(app.heartbeat_timer, 0));
}

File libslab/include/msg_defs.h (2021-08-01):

#pragma once
#include "mxgen.h"

////////////////////////////////////////////////////////////////////////////////
// IMU

// acceleration in units of (g)
// angular velocity in units of (rad/s)

#define TYPEDEF_QuaternionF(X, _) \
    X(float, qw, )                \
    X(float, qx, )                \
    X(float, qy, )                \
    X(float, qz, )
MXGEN(struct, QuaternionF)

#define TYPEDEF_Vector3F(X, _) \
    X(float, x, )              \
    X(float, y, )              \
    X(float, z, )
MXGEN(struct, Vector3F)

#define TYPEDEF_ImuMsg(X, _)           \
    X(QuaternionF, orientation, )      \
    X(Vector3F, linear_acceleration, ) \
    X(Vector3F, angular_velocity, )
MXGEN(struct, ImuMsg)

////////////////////////////////////////////////////////////////////////////////
// Motor

// position in units of (rad)
// velocity in units of (rad/s)
// torque in units of (Nm)

typedef enum {
    MOTOR_CONTROL_MODE_POSITION = 1 << 0,
    MOTOR_CONTROL_MODE_VELOCITY = 1 << 1,
    MOTOR_CONTROL_MODE_TORQUE = 1 << 2,
} MotorControlMode;

#define TYPEDEF_MotorInput(X, _) \
    X(float, position, )         \
    X(float, velocity, )         \
    X(float, torque, )           \
    X(uint8_t, control_mode, )
MXGEN(struct, MotorInput)

#define TYPEDEF_MotorEstimate(X, _) \
    X(float, position, )            \
    X(float, velocity, )
MXGEN(struct, MotorEstimate)

#define TYPEDEF_MotorMsg(X, _) \
    X(MotorInput, input, )     \
    X(MotorEstimate, estimate, )
MXGEN(struct, MotorMsg)

////////////////////////////////////////////////////////////////////////////////
// Gamepad

typedef enum {
    GAMEPAD_BUTTON_SELECT = 1 << 0,
    GAMEPAD_BUTTON_L3 = 1 << 1,
    GAMEPAD_BUTTON_R3 = 1 << 2,
    GAMEPAD_BUTTON_START = 1 << 3,

    GAMEPAD_BUTTON_UP = 1 << 4,
    GAMEPAD_BUTTON_RIGHT = 1 << 5,
    GAMEPAD_BUTTON_DOWN = 1 << 6,
    GAMEPAD_BUTTON_LEFT = 1 << 7,

    GAMEPAD_BUTTON_L2 = 1 << 8,
    GAMEPAD_BUTTON_R2 = 1 << 9,
    GAMEPAD_BUTTON_L1 = 1 << 10,
    GAMEPAD_BUTTON_R1 = 1 << 11,

    GAMEPAD_BUTTON_TRIANGLE = 1 << 12,
    GAMEPAD_BUTTON_CIRCLE = 1 << 13,
    GAMEPAD_BUTTON_CROSS = 1 << 14,
    GAMEPAD_BUTTON_SQUARE = 1 << 15,
} GamepadButton;

#define TYPEDEF_GamepadStick(X, _) \
    X(int8_t, x, )                 \
    X(int8_t, y, )
MXGEN(struct, GamepadStick)

#define TYPEDEF_GamepadMsg(X, _)   \
    X(uint16_t, buttons, )         \
    X(GamepadStick, left_stick, )  \
    X(GamepadStick, right_stick, ) \
    X(uint8_t, left_trigger, )     \
    X(uint8_t, right_trigger, )
MXGEN(struct, GamepadMsg)

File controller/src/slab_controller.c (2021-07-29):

#include "math_utils.h"
#include "slab_controller.h"

static void axis_remap(Vector3F* out, const Vector3F* in, const int8_t* remap) {
    for (int i = 0; i < 3; ++i) {
        int axis = remap[i] & 3;
        assert(axis < 3);
        ((float*) out)[i] = ((float*) in)[axis];
        if (remap[i] & AXIS_REMAP_NEG_FLAG) {
            ((float*) out)[i] *= -1;
        }
    }
}

static void slab_gamepad_input_update(Slab* slab) {
    enum { X, Y, RX, RY };
    // parse stick to [lx, ly, rx, ry] normalized to 1
    float sticks[4] = {0};
    for (int i = 0; i < 4; ++i) {
        if (ABS((&slab->gamepad.left_stick.x)[i]) >=
                slab->config.joystick_threshold) {
            sticks[i] = -((&slab->gamepad.left_stick.x)[i] + 0.5f) / 127.5f;
        }
    }
    // parse buttons to axis vector
    float buttons[4] = {
            GET_BIT(slab->gamepad.buttons, GAMEPAD_BUTTON_LEFT) -
                    GET_BIT(slab->gamepad.buttons, GAMEPAD_BUTTON_RIGHT),
            GET_BIT(slab->gamepad.buttons, GAMEPAD_BUTTON_UP) -
                    GET_BIT(slab->gamepad.buttons, GAMEPAD_BUTTON_DOWN),
            GET_BIT(slab->gamepad.buttons, GAMEPAD_BUTTON_SQUARE) -
                    GET_BIT(slab->gamepad.buttons, GAMEPAD_BUTTON_CIRCLE),
            GET_BIT(slab->gamepad.buttons, GAMEPAD_BUTTON_TRIANGLE) -
                    GET_BIT(slab->gamepad.buttons, GAMEPAD_BUTTON_CROSS),
    };
    // normalize button axis and scale by trigger
    for (int i = 0; i < 2; ++i) {
        float* axis = buttons + (2 * i);
        if (axis[X] != 0 && axis[Y] != 0) {
            float inv_norm = 1.0f / vec_norm(axis, 2);
            axis[X] *= inv_norm;
            axis[Y] *= inv_norm;
        }
        float trigger = (&slab->gamepad.left_trigger)[i] / 255.0f;
        axis[X] *= trigger;
        axis[Y] *= trigger;
    }
    // disable balance control with L1
    if (GET_BIT(slab->gamepad.buttons, GAMEPAD_BUTTON_L1)) {
        slab->state.balance_active = false;
    }
    // scale velocity input to max wheel speed
    float speed_scale =
            0.5f * slab->config.wheel_diameter * slab->config.max_wheel_speed;
    if (slab->state.balance_active) {
        speed_scale /= 4;
    }
    // map L-stick to velocity input (dpad overrides stick)
    float* velocity_input =
            buttons[X] == 0 && buttons[Y] == 0 ? sticks : buttons;
    slab->input.linear_velocity = velocity_input[Y] * speed_scale;
    slab->input.angular_velocity = velocity_input[X] * speed_scale /
                                   (0.5f * slab->config.wheel_distance);
    // map R-stick to velocity input (button overrides stick)
    float* legs_input =
            (buttons[RX] == 0 && buttons[RY] == 0 ? sticks : buttons) + 2;
    // leg position control logic
    const float leg_speed = 0.02f;
    for (int i = 0, sign = -1; i < 2; ++i, sign *= -1) {
        bool only_contact = slab->state.ground_contacts == i + 1;
        if (!GET_BIT(slab->gamepad.buttons, GAMEPAD_BUTTON_R1)) {
            slab->input.body_incline -= 0.5f * leg_speed * legs_input[Y] *
                                        SGN(slab->state.body_incline);
            int dir = slab->state.balance_active ? (only_contact ? 2 : -1) : 1;
            slab->input.leg_positions[i] +=
                    leg_speed * (legs_input[X] * (1 - only_contact) +
                                        legs_input[Y] * sign * dir);
            slab->input.leg_positions[i] = CLAMP(slab->input.leg_positions[i],
                    slab->config.min_leg_position,
                    slab->config.max_leg_position);
        } else if (!only_contact) {
            if (SQR(legs_input[X]) > SQR(legs_input[Y])) {
                LOW_PASS_FILTER(slab->input.body_incline,
                        SGN(slab->input.body_incline) * M_PI_2,
                        leg_speed * ABS(legs_input[X]));
                LOW_PASS_FILTER(slab->input.leg_positions[i],
                        SGN(legs_input[X]) * M_PI,
                        leg_speed * ABS(legs_input[X]));
            } else {
                LOW_PASS_FILTER(slab->input.body_incline,
                        (SGN(slab->input.body_incline) +
                                sign * SGN(legs_input[Y])) *
                                M_PI_2,
                        0.5f * leg_speed * ABS(legs_input[Y]));
                LOW_PASS_FILTER(slab->input.leg_positions[i],
                        sign * SGN(legs_input[Y]) * M_PI_2,
                        leg_speed * ABS(legs_input[Y]));
            }
        }
    }
}

static void slab_differential_drive_update(
        Slab* slab, float v_lin, float v_ang) {
    const float r = slab->config.wheel_diameter / 2;
    const float R = slab->config.wheel_distance / 2;
    const float v_max = slab->config.max_wheel_speed;
    float left_wheel_speed = (v_lin - v_ang * R) / r;
    float right_wheel_speed = (v_lin + v_ang * R) / r;
    left_wheel_speed = CLAMP(left_wheel_speed, -v_max, v_max);
    right_wheel_speed = CLAMP(right_wheel_speed, -v_max, v_max);
    uint8_t legs = slab->state.ground_contacts;
    slab->motors[MOTOR_ID_FRONT_LEFT_WHEEL].input.velocity =
            (legs & 1) ? left_wheel_speed : 0;
    slab->motors[MOTOR_ID_FRONT_RIGHT_WHEEL].input.velocity =
            (legs & 1) ? right_wheel_speed : 0;
    slab->motors[MOTOR_ID_BACK_LEFT_WHEEL].input.velocity =
            (legs & 2) ? left_wheel_speed : 0;
    slab->motors[MOTOR_ID_BACK_RIGHT_WHEEL].input.velocity =
            (legs & 2) ? right_wheel_speed : 0;
    // velocity control mode
    for (int i = 0; i < 4; ++i) {
        slab->motors[MOTOR_ID_FRONT_LEFT_WHEEL + i].input.control_mode =
                MOTOR_CONTROL_MODE_VELOCITY;
    }
}

static void slab_ground_controller_update(Slab* slab) {
    slab_differential_drive_update(
            slab, slab->input.linear_velocity, slab->input.angular_velocity);
    for (int i = 0; i < 2; ++i) {
        slab->motors[i].input.position = CLAMP(slab->input.leg_positions[i],
                slab->config.min_leg_position, slab->config.max_leg_position);
        slab->motors[i].input.control_mode = MOTOR_CONTROL_MODE_POSITION;
    }
}
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

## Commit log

2021-06-06 renamed odrive readme
2021-06-06 updated urdf and odrive readme
    [robot.urdf]
2021-06-07 working imu dmp
2021-06-08 added draft bom
    [bom.ods]
2021-06-12 upped IMU DMP to 100Hz
2021-06-12 added limit switch to bom
    [bom.ods]
2021-06-13 better IMU fifo logic
2021-06-14 cleaned up mpu6050 interface
    [bom.ods]
2021-06-17 tested can working
    [bom.ods]
2021-06-21 addded motor msgs
2021-06-25 added odrive helpers
2021-07-06 fixed max wheel speed
    [slab_controller.c]
2021-07-07 added ctype print method
2021-07-07 added sim motor feedback
2021-07-07 added leg control
2021-07-07 swapped robot front and back
    [robot.urdf]
2021-07-11 fixed rotation matrix conversion
    [slab_controller.c]
2021-07-12 added wheel_to_wheel
2021-07-13 added ground contact state
2021-07-14 added ground contact hysterisis
2021-07-14 added body velocity feedback
2021-07-16 fixed controls incline flip
    [slab_controller.c]
2021-07-26 setup legs odrive
2021-07-28 more generic motor interface
2021-07-29 updated to odrive_can component and some cleanup
2021-07-29 added homing on start button
2021-07-29 added better odrive error reporting
    [main.c]
2021-07-29 implemented motors input update
2021-08-01 changed gamepad buttons to masks instead of offsets
2021-08-01 ps3 controller led on connect
2021-08-02 fixed odrive error get
    [main.c]
2021-08-02 display error on gamebad controller LED
    [main.c]
2021-08-04 simplied plotting sample fetch
2021-08-04 fixed minor serial json selection out of bounds bug
    [serial_json.py]
2021-08-04 chaned to 921600 baud, and fixed serial json lag
    [main.c, serial_json.py]
2021-08-04 changed error flags to union
    [main.c, serial_json.py]
2021-08-05 fixed ps3 rumble, clear odrive errors on start
    [main.c]
2021-08-05 motor testing WIP
2021-08-05 fixed position input scaling
    [main.c]
2021-08-05 legs testing WIP
2021-08-05 fixed motors init idle state
    [main.c]
2021-08-05 odrive request idle instead of estop
2021-08-05 simplified leg position input logic
2021-08-07 press select button to clear errors
    [main.c]
2021-08-07 added homing timeout
2021-08-07 added runtime endstop handling
2021-08-07 added can error flag
    [main.c]
2021-08-08 tested and fixed led heartbeat
    [main.c]
2021-08-08 fixed gamepad L1 race condition
    [main.c, slab.c]
2021-08-08 legs tested working
2021-08-16 retuned leg motors
2021-08-19 updated leg motor tunings
2021-08-25 updated front wheel motor calibration
2021-08-26 working wheel motors control
2021-08-30 added gamepad estop button
2021-08-30 updated gear box ratio
2021-08-31 invert balance toggle button
    [main.c]
2021-09-04 added wifi ap
    [partitions.csv]
2021-09-07 added http server
    [partitions.csv]
2021-09-09 used start button to home and clear errors
    [main.c]
2021-09-13 fixed status msg queing
    [main.c]
2021-09-13 excluded watchdog timeout from error flags
    [main.c]
2021-09-15 updated hub motor tunings
2021-09-29 fixed watchdog error exclude
    [main.c]
